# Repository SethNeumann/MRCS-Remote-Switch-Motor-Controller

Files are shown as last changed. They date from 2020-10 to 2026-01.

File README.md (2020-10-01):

# REPO NAME: MRCS-Remote-Switch-Motor-Controller

The Remote Stall Motor Controller is designed to mount on a Circuitron(r) Tortoise slow motion switch machine and provides bi-polar control with a single logic level line, such as provided by a cpNode, IOX16/32, SMINI, DOUT, or SPST toggle switch. The RSMC can also be used to control the MP1 switch motor.

## License: Creative Commons Attribution-NonCommercial-ShareAlike

MRCS-Remote-Switch-Motor-Controller

The Remote Stall Motor Controller is designed to mount on a Circuitron(r) Tortoise slow motion switch machine and provides bi-polar control with a single logic level line, such as provided by a cpNode, IOX16/32, SMINI, DOUT, or SPST toggle switch. The RSMC can also be used to control the MP1 switch motor.

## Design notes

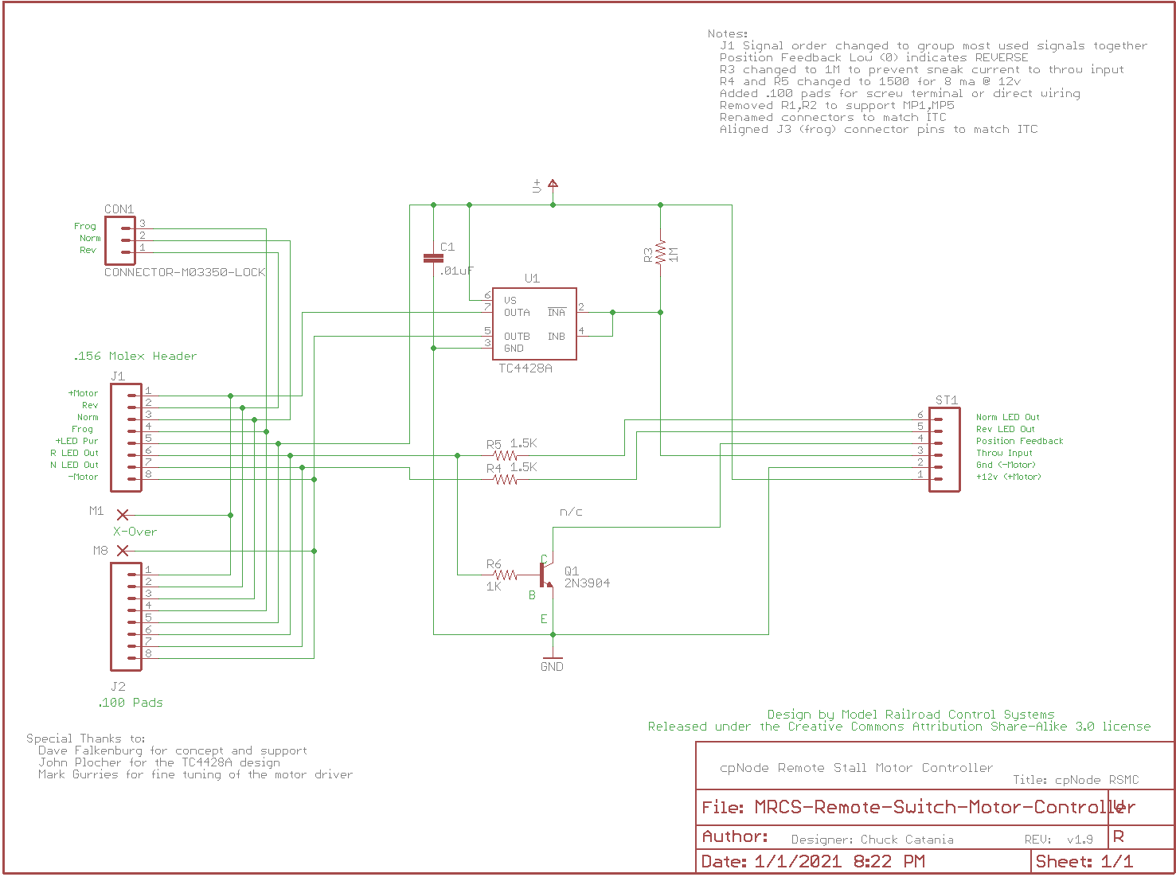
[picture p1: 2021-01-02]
RSMC Schematic Drawing.png

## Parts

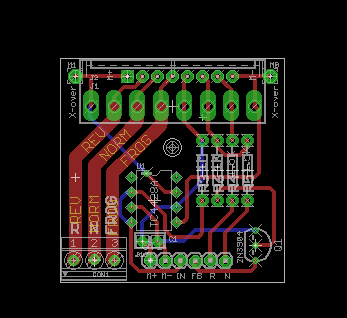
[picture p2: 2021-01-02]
RSMC Parts Layout.png

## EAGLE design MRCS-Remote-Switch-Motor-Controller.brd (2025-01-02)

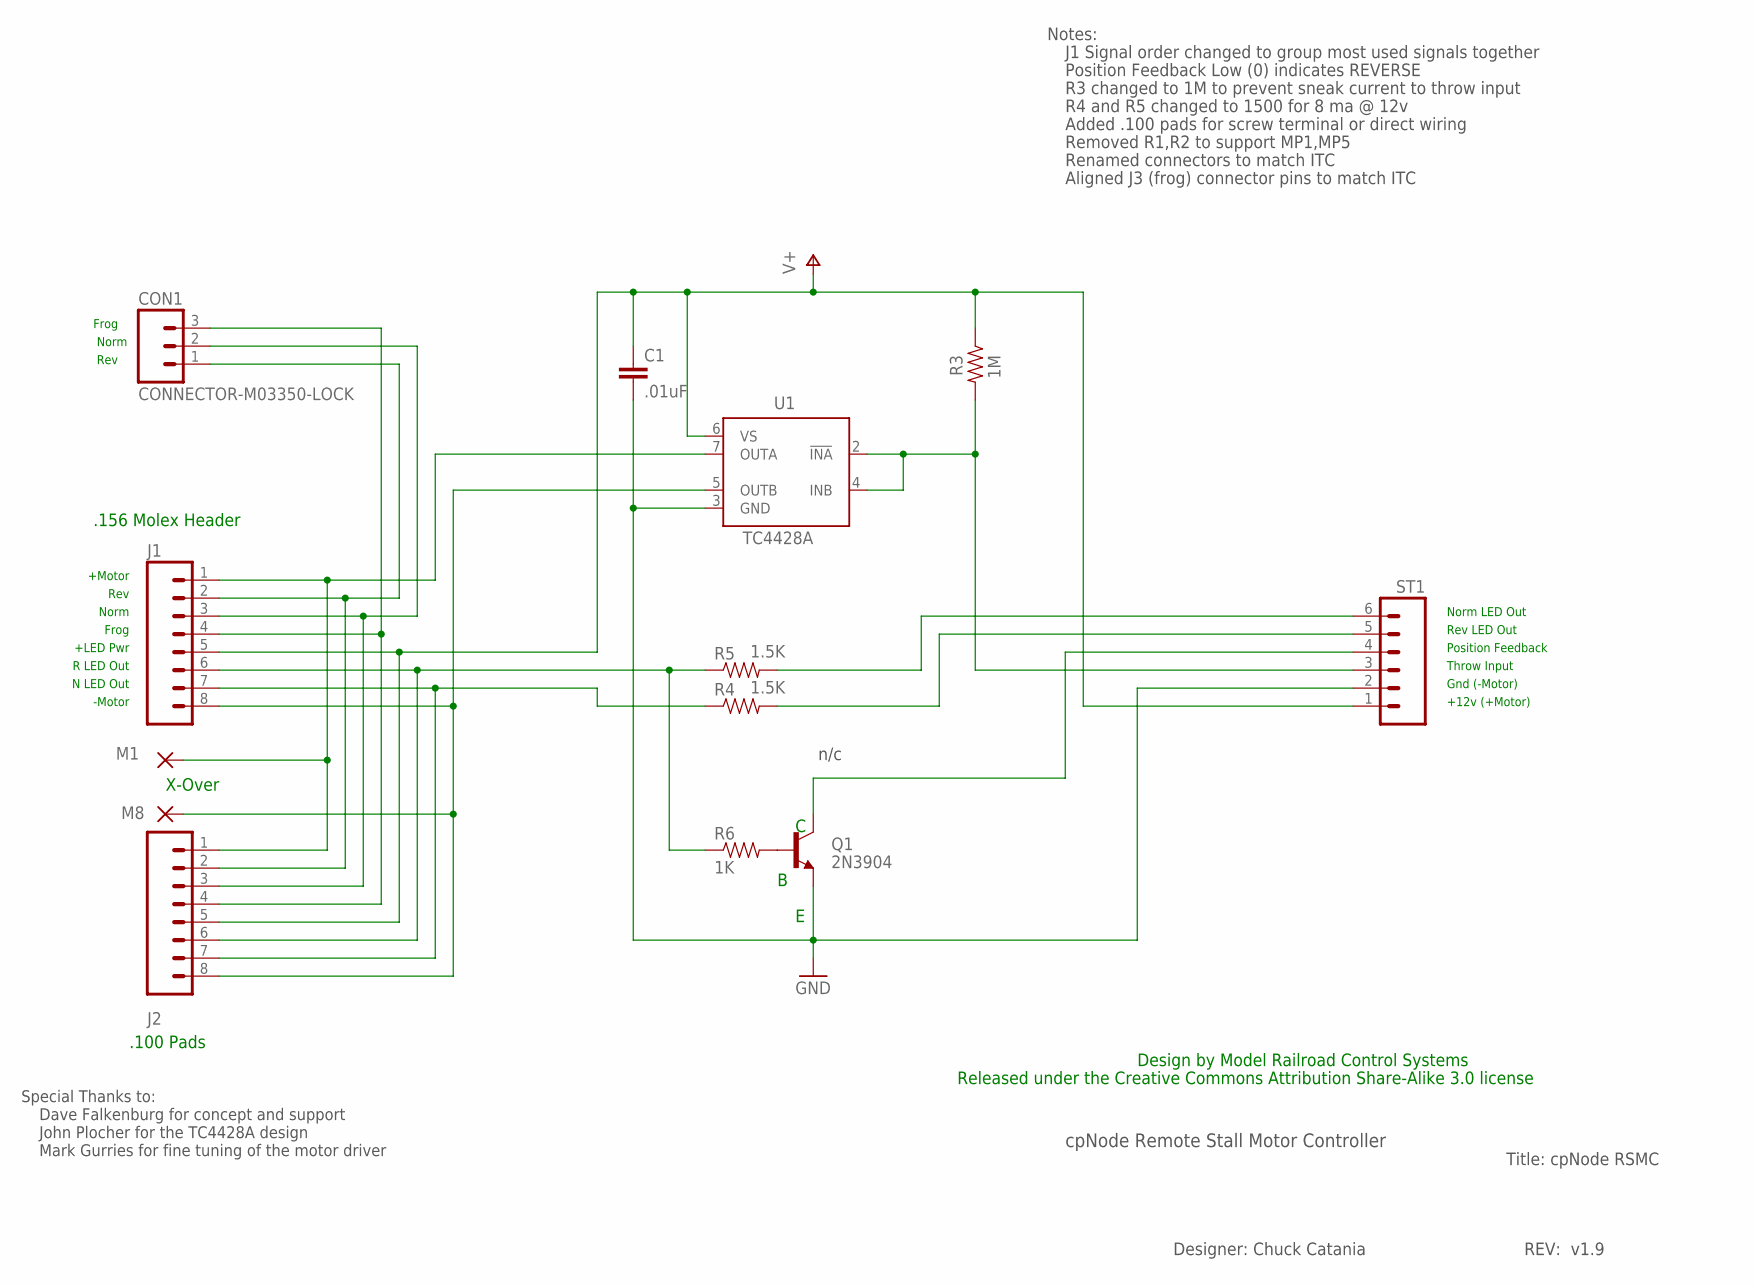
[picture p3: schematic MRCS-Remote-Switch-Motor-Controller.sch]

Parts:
C1: .01uF; CAP-PTH-SMALLEZ
CON1: CONNECTOR-M03350-LOCK; 1751251
J1: J1; KK-156-8-F
J2: J2; 1X08_PIN1_NO_SILK
M1, M8: WIREPAD2,54/1,1; 2,54/1,1
Q1: 2N3904; TO-92-MS013
R3: 1M; AXIAL-0.4-RES
R4, R5: 1.5K; AXIAL-0.4-RES
R6: 1K; AXIAL-0.4-RES
ST1: M06LOCK; 1X06_LOCK
U1: TC4428A; DIL08

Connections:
FROG: CON1.3, J1.4, J2.4
GND: C1.2, Q1.1 (E), ST1.2, U1.3 (GND)
M+: J1.1, J2.1, M1.1, U1.7 (OUTA)
M-: J1.8, J2.8, M8.1, U1.5 (OUTB)
unnamed: Q1.3 (C), ST1.4
unnamed: R4.P$2 (2), ST1.5
unnamed: Q1.2 (B), R6.P$2 (2)
unnamed: R5.P$2 (2), ST1.6
unnamed: R3.P$2 (2), ST1.3, U1.2 (!INA), U1.4 (INB)
N-LED: J1.7, J2.7, R4.P$1 (1)
NORM: CON1.2, J1.3, J2.3
R-LED: J1.6, J2.6, R5.P$1 (1), R6.P$1 (1)
REV: CON1.1, J1.2, J2.2
V+: C1.1, J1.5, J2.5, R3.P$1 (1), ST1.1, U1.6 (VS)

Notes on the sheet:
Norm
Rev
+12v (+Motor)
Gnd (-Motor)
Norm LED Out
Rev LED Out
Frog
+Motor
-Motor
Throw Input
+LED Pwr
R LED Out
N LED Out
.156 Molex Header
Position Feedback
cpNode Remote Stall Motor Controller
Title: cpNode RSMC
Designer: Chuck Catania
REV: v1.9
n/c
Special Thanks to:
John Plocher for the TC4428A design
Dave Falkenburg for concept and support
Mark Gurries for fine tuning of the motor driver
Notes:
Position Feedback Low (0) indicates REVERSE
R4 and R5 changed to 1500 for 8 ma @ 12v
J1 Signal order changed to group most used signals together
R3 changed to 1M to prevent sneak current to throw input
Frog
.100 Pads
Added .100 pads for screw terminal or direct wiring
X-Over
Removed R1,R2 to support MP1,MP5
Renamed connectors to match ITC
Aligned J3 (frog) connector pins to match ITC
Released under the Creative Commons Attribution Share-Alike 3.0 license
Design by Model Railroad Control Systems

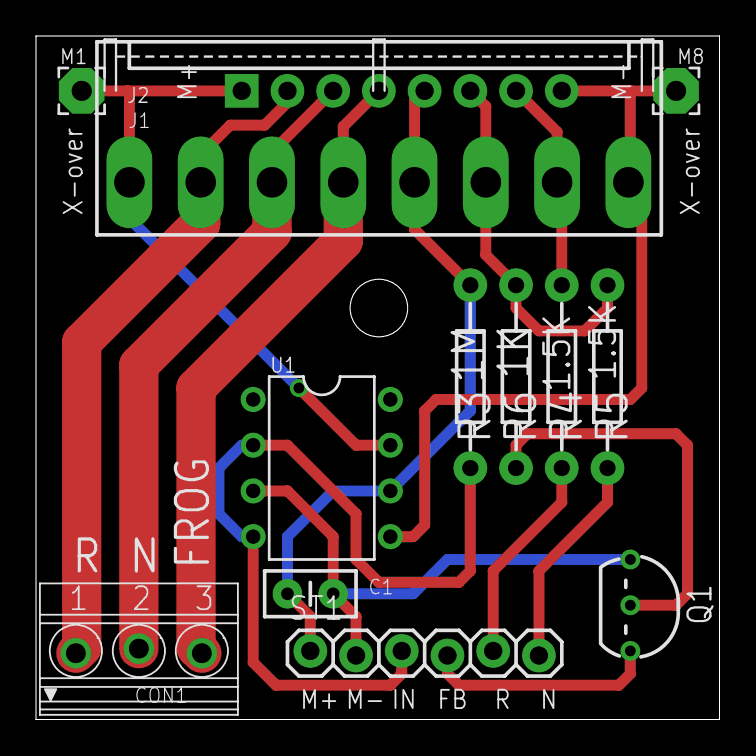
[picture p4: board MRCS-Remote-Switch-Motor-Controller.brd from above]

Board: 2 copper layers, 38.0 x 38.0 mm, 15 parts (0 on the bottom side), 14 nets.

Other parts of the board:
U$1: MRCSLOGOBTM
U$2: CA-PROP65WARNING

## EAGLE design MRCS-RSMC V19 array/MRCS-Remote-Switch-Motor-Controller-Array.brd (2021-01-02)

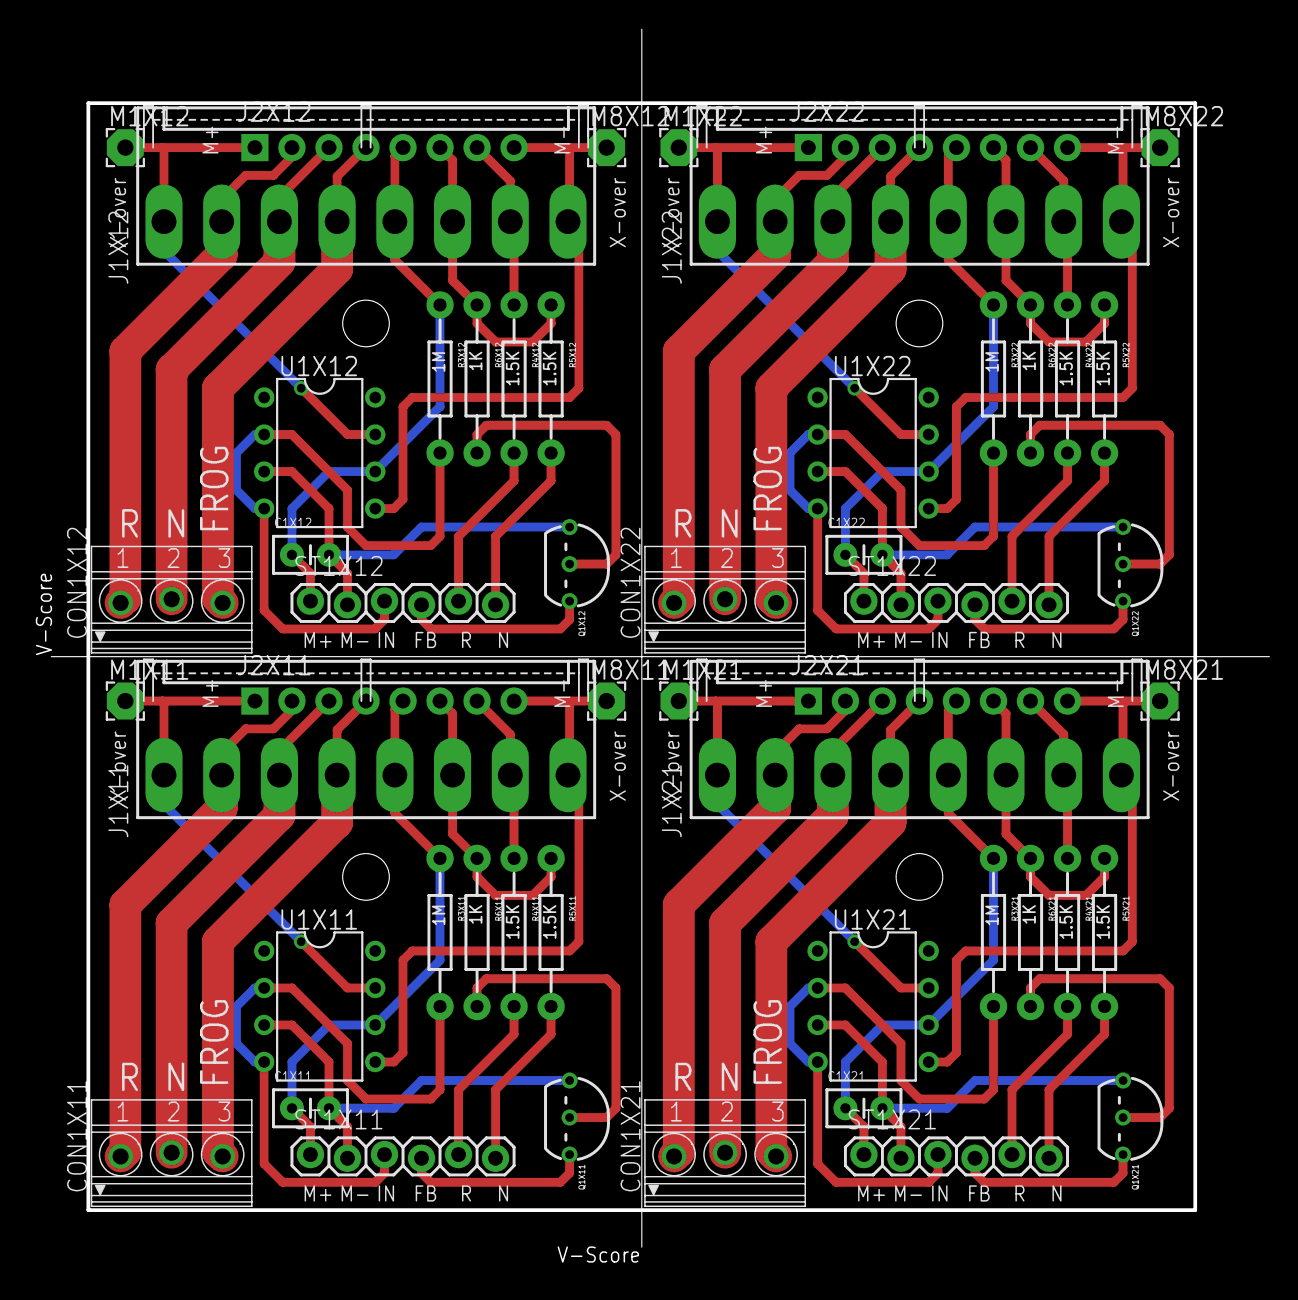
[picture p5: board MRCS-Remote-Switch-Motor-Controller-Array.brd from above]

Board: 2 copper layers, 75.9 x 75.9 mm, 60 parts (0 on the bottom side), 56 nets.

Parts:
C1X11, C1X12, C1X21, C1X22: .01uF; CAP-PTH-SMALLEZ
CON1X11, CON1X12, CON1X21, CON1X22: CONNECTOR-M03350-LOCK; 1751251
J1X11, J1X12, J1X21, J1X22: J1; KK-156-8-F
J2X11, J2X12, J2X21, J2X22: J2; 1X08_PIN1_NO_SILK
M1X11, M1X12, M1X21, M1X22, M8X11, M8X12, M8X21, M8X22: WIREPAD2,54/1,1; 2,54/1,1
Q1X11, Q1X12, Q1X21, Q1X22: 2N3904; TO-92-MS013
R3X11, R3X12, R3X21, R3X22: 1M; AXIAL-0.4-RES
R4X11, R4X12, R4X21, R4X22, R5X11, R5X12, R5X21, R5X22: 1.5K; AXIAL-0.4-RES
R6X11, R6X12, R6X21, R6X22: 1K; AXIAL-0.4-RES
ST1X11, ST1X12, ST1X21, ST1X22: 1X06_LOCK
U1X11, U1X12, U1X21, U1X22: TC4428A; DIL08
U$1X11, U$1X12, U$1X21, U$1X22: MRCSLOGOBTM
U$2X11, U$2X12, U$2X21, U$2X22: CA-PROP65WARNING

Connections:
FROGX11: CON1X11.3, J1X11.4, J2X11.4
FROGX12: CON1X12.3, J1X12.4, J2X12.4
FROGX21: CON1X21.3, J1X21.4, J2X21.4
FROGX22: CON1X22.3, J1X22.4, J2X22.4
GNDX11: C1X11.2, Q1X11.1, ST1X11.2, U1X11.3
GNDX12: C1X12.2, Q1X12.1, ST1X12.2, U1X12.3
GNDX21: C1X21.2, Q1X21.1, ST1X21.2, U1X21.3
GNDX22: C1X22.2, Q1X22.1, ST1X22.2, U1X22.3
M+X11: J1X11.1, J2X11.1, M1X11.1, U1X11.7
M+X12: J1X12.1, J2X12.1, M1X12.1, U1X12.7
M+X21: J1X21.1, J2X21.1, M1X21.1, U1X21.7
M+X22: J1X22.1, J2X22.1, M1X22.1, U1X22.7
M-X11: J1X11.8, J2X11.8, M8X11.1, U1X11.5
M-X12: J1X12.8, J2X12.8, M8X12.1, U1X12.5
M-X21: J1X21.8, J2X21.8, M8X21.1, U1X21.5
M-X22: J1X22.8, J2X22.8, M8X22.1, U1X22.5
unnamed: Q1X11.3, ST1X11.4
unnamed: Q1X12.3, ST1X12.4
unnamed: Q1X21.3, ST1X21.4
unnamed: Q1X22.3, ST1X22.4
unnamed: R4X11.P$2, ST1X11.5
unnamed: R4X12.P$2, ST1X12.5
unnamed: R4X21.P$2, ST1X21.5
unnamed: R4X22.P$2, ST1X22.5
unnamed: Q1X11.2, R6X11.P$2
unnamed: Q1X12.2, R6X12.P$2
unnamed: Q1X21.2, R6X21.P$2
unnamed: Q1X22.2, R6X22.P$2
unnamed: R5X11.P$2, ST1X11.6
unnamed: R5X12.P$2, ST1X12.6
unnamed: R5X21.P$2, ST1X21.6
unnamed: R5X22.P$2, ST1X22.6
unnamed: R3X11.P$2, ST1X11.3, U1X11.2, U1X11.4
unnamed: R3X12.P$2, ST1X12.3, U1X12.2, U1X12.4
unnamed: R3X21.P$2, ST1X21.3, U1X21.2, U1X21.4
unnamed: R3X22.P$2, ST1X22.3, U1X22.2, U1X22.4
N-LEDX11: J1X11.7, J2X11.7, R4X11.P$1
N-LEDX12: J1X12.7, J2X12.7, R4X12.P$1
N-LEDX21: J1X21.7, J2X21.7, R4X21.P$1
N-LEDX22: J1X22.7, J2X22.7, R4X22.P$1
NORMX11: CON1X11.2, J1X11.3, J2X11.3
NORMX12: CON1X12.2, J1X12.3, J2X12.3
NORMX21: CON1X21.2, J1X21.3, J2X21.3
NORMX22: CON1X22.2, J1X22.3, J2X22.3
R-LEDX11: J1X11.6, J2X11.6, R5X11.P$1, R6X11.P$1
R-LEDX12: J1X12.6, J2X12.6, R5X12.P$1, R6X12.P$1
R-LEDX21: J1X21.6, J2X21.6, R5X21.P$1, R6X21.P$1
R-LEDX22: J1X22.6, J2X22.6, R5X22.P$1, R6X22.P$1
REVX11: CON1X11.1, J1X11.2, J2X11.2
REVX12: CON1X12.1, J1X12.2, J2X12.2
REVX21: CON1X21.1, J1X21.2, J2X21.2
REVX22: CON1X22.1, J1X22.2, J2X22.2
V+X11: C1X11.1, J1X11.5, J2X11.5, R3X11.P$1, ST1X11.1, U1X11.6
V+X12: C1X12.1, J1X12.5, J2X12.5, R3X12.P$1, ST1X12.1, U1X12.6
V+X21: C1X21.1, J1X21.5, J2X21.5, R3X21.P$1, ST1X21.1, U1X21.6
V+X22: C1X22.1, J1X22.5, J2X22.5, R3X22.P$1, ST1X22.1, U1X22.6

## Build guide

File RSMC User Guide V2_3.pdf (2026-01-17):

# Remote Stall Motor Controller (RSMC) User Guide

## Revision v2.3 01/16/2026

Introduction
The RSMC is designed to provide the control functions needed for local or remote operation of a turnout for various styles of turnout motors. The RSMC provides LED outputs with onboard current limiting resistors for route and switch lock status.

Revision History
v2.1 | 07/07/2017 | CC
v1.4 | 06/08/2015 | CC
v1.3 | 04/17/2015 | CC
v1.2 | 12/26/2014 | CC
v1.1 | 04/16/2014 | CC
v1.0 | 01/29/2014 | CC
V2.2 | 01/01/2025 | SN
V2.3 | 01/16/2026 | SN

Model Railroad Control Systems www.modelrailroadcontrolsystems.com

Seth Neumann, sales@modelrailroadcontrolsystems.com Chuck Catania, (deceased)

Page 2 of 10

# Table of Contents

## Table of Contents

Model Railroad Control Systems | 1

### 1. SYSTEM OVERVIEW | 3 2. CONNECTION EXAMPLES | 5 3. CONTROL PORTS - INPUT AND OUTPUT | 5 4. TURNOUT MOTOR CONNECTIONS | 5

4.1.Circuitron Tortoise/Switchmaster Stall Motor | 5
4.2.Tortoise Switch Motor Connector | 5
4.3.MP1/MP4/MP5/MP10 Connection | 6

### 5. REVERSING MOTOR CONNECTIONS | 7 6. MOTOR CONNECTION OPTIONS | 7 7. STALL MOTOR INTERFACE | 8 8. ASSEMBLY | 10

Figure 1- RSMC Block Diagram | 3
Figure 2- Remote Stall Motor Controller Component Locations (note input designations over J1) | 4
Figure 3- RSMC Connection Examples | 5
Figure 4- Stall Motor Connections | 6
Figure 5- Tortoise Pin Assignments | 6
Figure 6- MP4/MP10 Connections | 7
Figure 7- RSMC Configurations | 8
Figure 8- Bill of Materials | 9

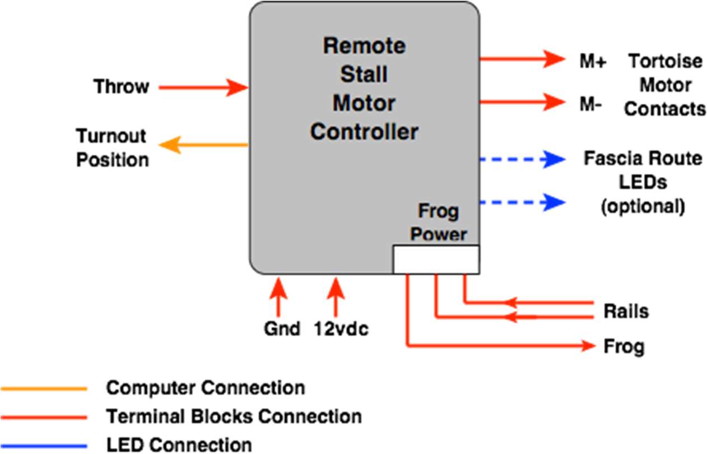
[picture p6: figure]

Page 3 of 10

## 1. SYSTEM OVERVIEW

The Remote Stall Motor Controller (RSMC) is designed to operate with stall motor style turnout motors (Tortoise, Switchmaster), switch turnout motors (MP1/MP4/MP5/MP10, Fulgurex)

The ITC has the following features: - 8 position motor pads for a .156" Molex connector, .156" edge connector, or .100" (2.54mm) - Stall motor power input, 9-12 Vdc - Throw input port - Turnout position feedback output - Route LED ports, Normal/Reverse (Common Cathode, Sourcing) - Frog power routing using external switch contacts (Tortoise, Switchmaster™)

Pads for connection to a Tortoise stall motor are .156" for Molex™. The pad spacing also mates to a standard 8 position .156" edge connector. Right angle or straight header pins can be soldered directly to the Tortoise edge connector and mate to a Molex connector on the ITC.

Pads for connection to .100" (2.54mm) screw terminal blocks or other .100" spaced connectors are parallel connected to the .156" pads.

Figure 1- RSMC Block Diagram

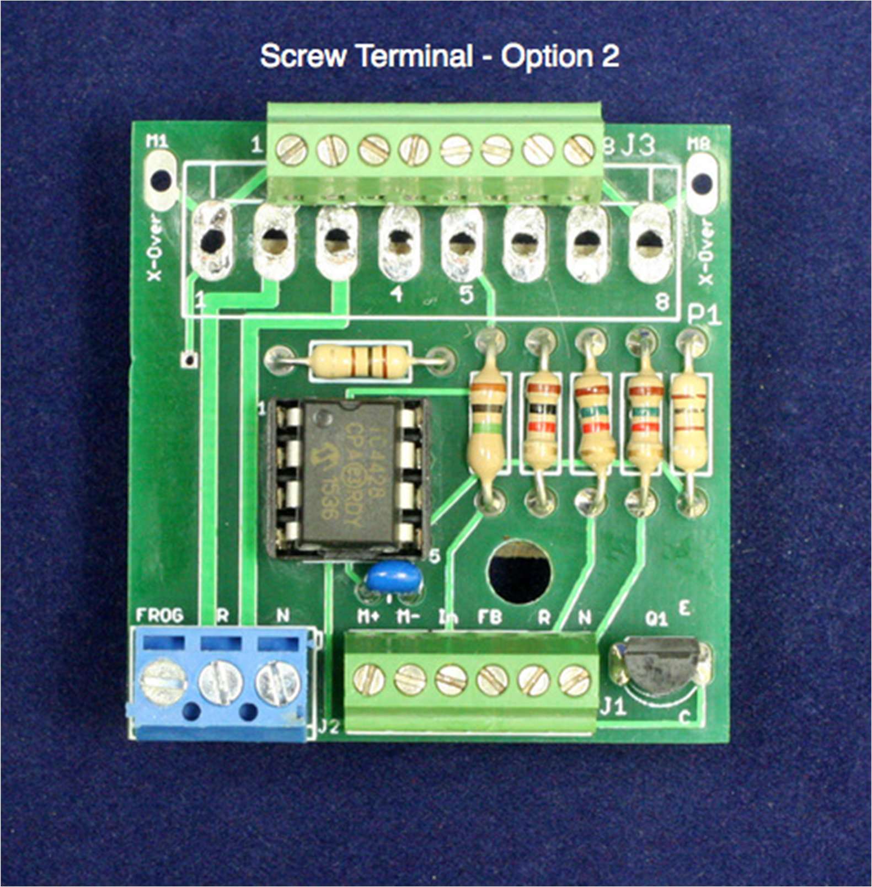
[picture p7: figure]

Page 4 of 10

Figure 2- Remote Stall Motor Controller Component Locations (note input designations over J1)

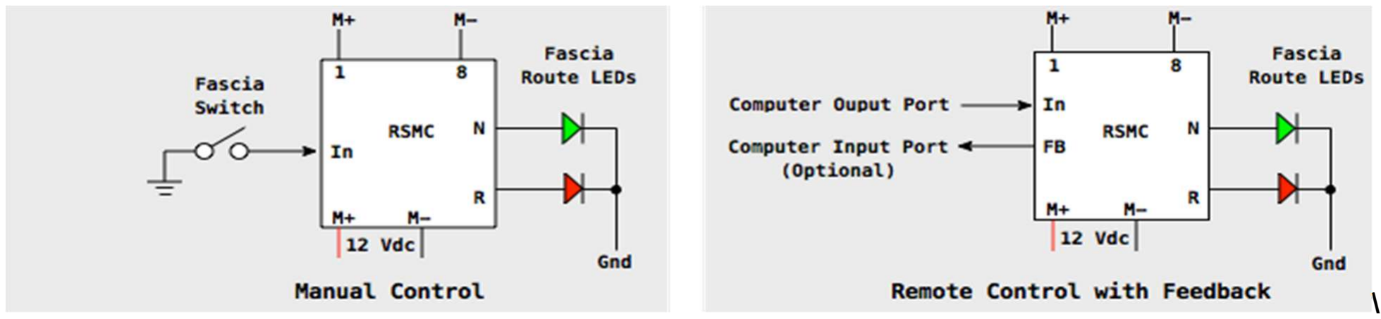
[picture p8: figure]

Page 5 of 10

## 2. CONNECTION EXAMPLES

\
Figure 3- RSMC Connection Examples

## 3. CONTROL PORTS - INPUT AND OUTPUT

The RSMC has one input port and one output port used for controlling a turnout motor. Each input is intended to provide an equivalent control line, which may be found in prototype turnout control installations. Throw In - (Input) This input controls the operation of the turnout from a local source like as fascia toggle switch. A Low input will throw the turnout to the opposite position.
Turnout Position (Feedback) - (Output) This output reflects the last commanded position of the turnout. This output is normally connected to a computer input port for monitoring by control software. A High state indicates the Normal route is selected, a Low state, the Reverse route is selected. The position of a turnout within a signaled section is normally used to set the correct signal aspect in ABS/CTC environments.
Route LEDs - The RSMC provides direct drive for status LEDs. The M+ input voltage is routed through one set of contacts in the Tortoise. The LED outputs are internally routed through the external switch contacts. Normally, the LEDs are mounted on fascia panels. Two signals are provided which are intended to drive fascia mounted LEDS to indicate which route (Normal/Reverse) is active. Limiting resistors are provided onboard for the LEDs.

## 4. TURNOUT MOTOR CONNECTIONS

Connection to a turnout motor is through the 8-position connector, J1 or J2. Pin 1 and Pin 8 are the motor voltage outputs. The RSMC reverses the polarity of the output pins based on the state of the onboard throw signal. Various types of turnout motors can be interfaced to the ITC.

### 4.1. Circuitron Tortoise/Switchmaster Stall Motor

Direct connection to stall motor style turnout motors. Changing the motor voltage polarity changes direction of throw bar.

### 4.2. Tortoise Switch Motor Connector

Direct connection to a Tortoise stall motor is done through the .156" pads. The pads can have a .156" female Molex connector or an 8-position card edge connector. A right angle Molex male connector can be easily soldered to the edge finger pads on the Tortoise stall motor.
If hardwired connections to a turnout motor is desired, a set of .100" (2.54 mm) spaced pads are

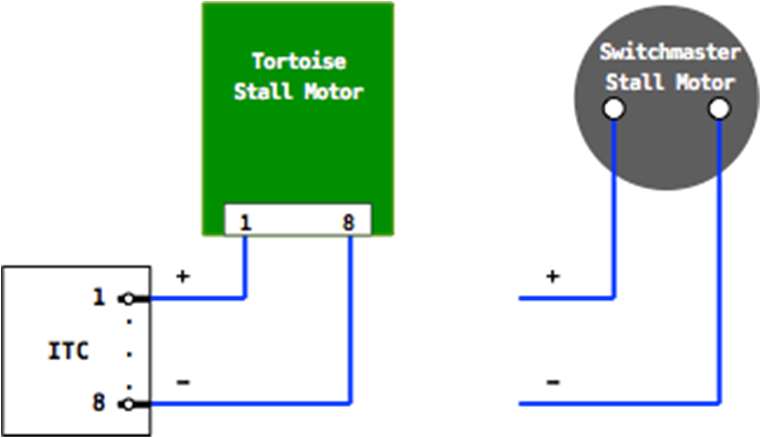
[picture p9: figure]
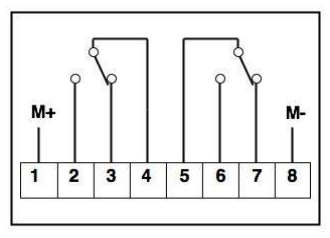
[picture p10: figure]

Page 6 of 10

provided for a screw terminal block, male header pins, or direct solder. These pads are connected to the .156" pads.

Pins 2,3 and 4 are connected to the Frog power connector.

Figure 4- Stall Motor Connections

Figure 5- Tortoise Pin Assignments

### 4.3. MP1/MP4/MP5/MP10 Connection

The MP series motors by MTB are end stop style turnout motors.

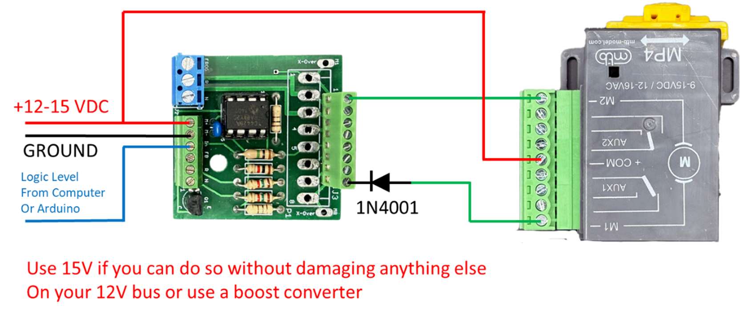
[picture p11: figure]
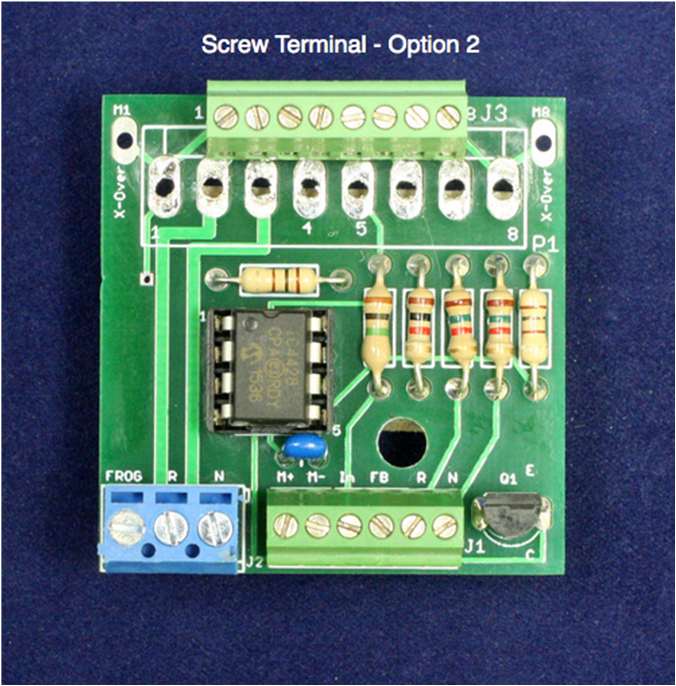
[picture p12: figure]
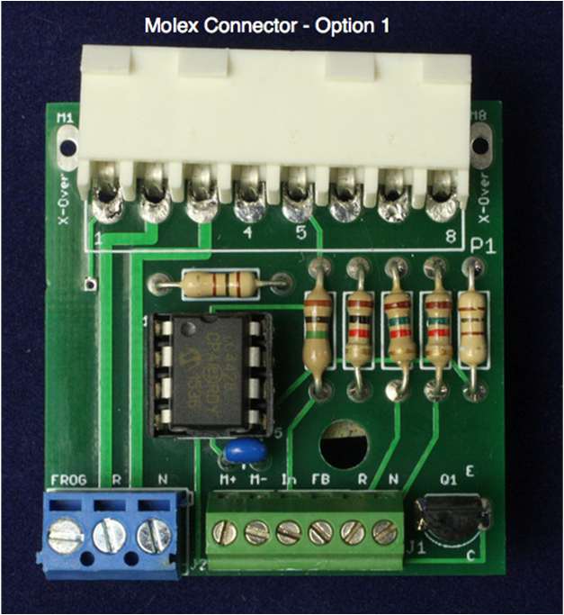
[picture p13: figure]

Page 7 of 10

Figure 6- MP4/MP10 Connections

## 5. REVERSING MOTOR CONNECTIONS

If the turnout motor, on power up, does not align to the desired default route, flip the RSMC over when using the Molex connector, or rotate the RSMC 180 degrees if using the card edge connector, or swap the motor wires (pin 1 and 8) on the .100" output screw terminal block.

## 6. MOTOR CONNECTION OPTIONS

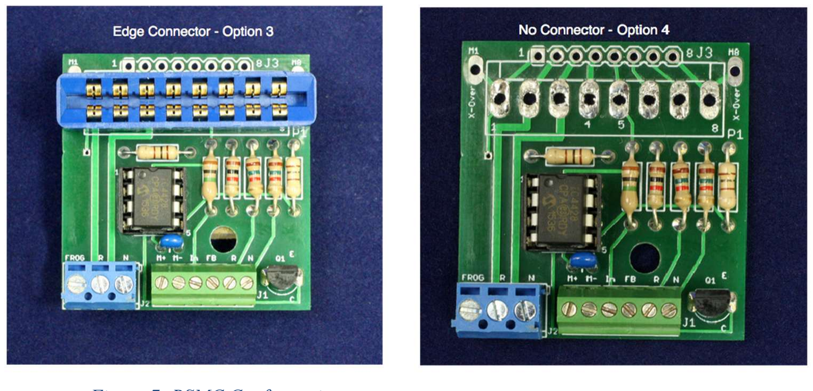
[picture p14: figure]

Page 8 of 10

Figure 7- RSMC Configurations

## 7. STALL MOTOR INTERFACE

The RSMC drives the stall motor through a MOSFET chip connected to the motor voltage. When the Throw Input pin is grounded, the polarity to the Tortoise motor is reversed, and the motor moves to the opposite position. A SPST toggle switch, connected between the motor minus terminal and the Throw Input pin, is all that is need to operate the RSMC. On power up, the RSMC drives the Tortoise to a default position. If the power up route of the connected turnout is not what is desired, flip the RSMC and plug in upside down.

Note: Dc voltage input for the motor, must be connected to the +motor, -motor with the correct polarity.

Turnout position feedback is provided from the Position Feedback pin. This is an open collector output and is set low (zero) when the reverse switch contacts are active.

Route LEDs are driven by one set of internal contacts in the Tortoise. Common Cathode (sourcing) LED connections are supported. Stall motor voltage is routed from the external contacts through onboard limiting resistors to the terminal strip. Resistor values for R4/R5 can be selected to adjust the brightness of the LEDs. The route LEDs, if mounted on a fascia panel, will only light if the internal switch contacts mate correctly.

The other set of external switch contacts provide connections for routing power to an isolated turnout frog. Heavier traces are routed to a 3.5mm screw terminal for the frog connections.BILL OF MATERIALS

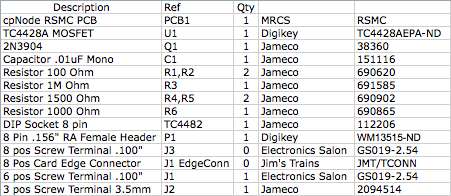
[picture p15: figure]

Page 9 of 10

Figure 8- Bill of Materials

Page 10 of 10

## 8. ASSEMBLY

[ ] All of the components are through-hole technology with wire leads. A useful tool is a lead bender for forming the leads at 90 degrees for easy insertion into the pad holes. Start with inserting the lower height components.

[ ] Install the IC socket for U1. Orient the socket with pin 1 shown on the silk screen.

[ ] Install resistor R3 (1 Meg ohms)

[ ] Install resistors R4,R5 (1500 ohms). Select value to adjust LED brightness.

[ ] Install resistor R6 (1000 ohms)

[ ] Install the bypass capacitor C1 (.1uF)

[ ] Install transistor Q1, (2N3904). Orient the transistor to the silkscreen markings.
[ ] Install the 6 position, .100" screw terminal block, ST1 [ ] Install the 8 position, .156" Molex connector, J1 OR
[ ] Install the 8 position,.156" Edge Connector, J1 OR
[ ] Install the 8 position, .100" screw terminal block, J2

[ ] Install the 3 position, 3.5 mm screw terminal block, J3

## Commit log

2020-10-01 moved to github
    moved to GitHub
    [EagleTemplate-new.brd, EagleTemplate-new.sch, MRCS-Remote-Switch-Motor-Controller.brd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]
2020-12-20 minior changes to labels
    changes for legibility
    [MRCS-Remote-Switch-Motor-Controller.brd]
2020-12-24 Added work files to gitignore and label changes
    Added work files to gitignore and made labels on board 56 mil rather than 32 so they can be read more easily
    [MRCS-Remote-Switch-Motor-Controller.brd, MRCS-Remote-Switch-Motor-Controller.sch]
2021-01-02 Updated Documentation and created pdf
    documentation
    [MRCS-Remote-Switch-Motor-Controller-Array.brd, MRCS-Remote-Switch-Motor-Controller.brd, MRCS-Remote-Switch-Motor-Controller.sch]
2025-01-02 adds MP4 MP10
    long overdue update of RSMC instructions, corrects input terminals, adds MP4, MP10. Format changes
    [MRCS-Remote-Switch-Motor-Controller-Array.brd, MRCS-Remote-Switch-Motor-Controller.brd]

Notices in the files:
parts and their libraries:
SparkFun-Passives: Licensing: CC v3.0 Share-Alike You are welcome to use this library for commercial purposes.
